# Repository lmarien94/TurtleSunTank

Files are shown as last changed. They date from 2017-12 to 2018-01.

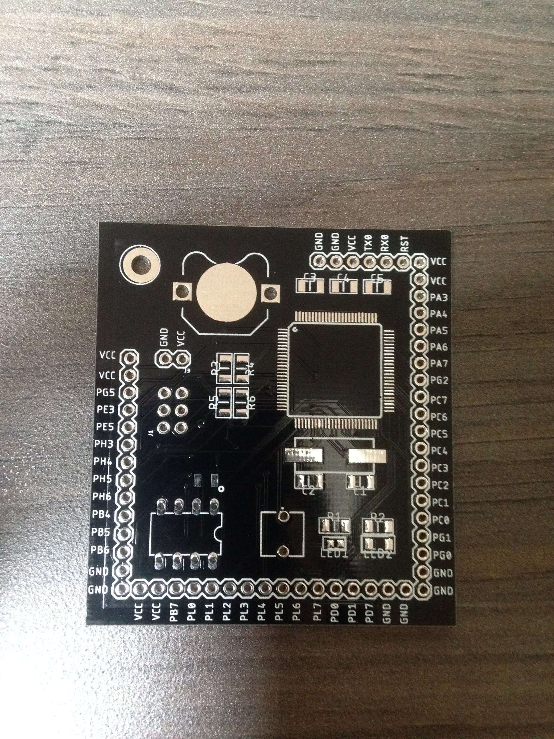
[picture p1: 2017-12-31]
Pictures/PCB before soldering.JPG

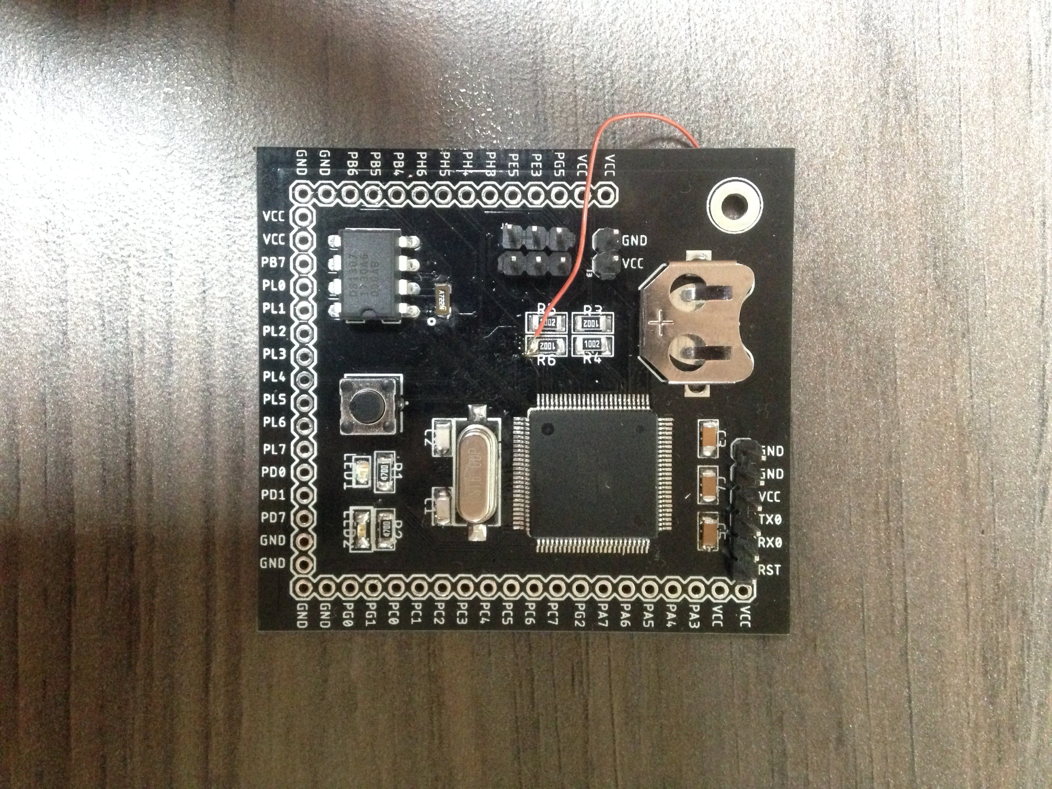
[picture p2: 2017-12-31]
Pictures/PCB after soldering.JPG

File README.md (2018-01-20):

# TurtleSunTank
Since reptiles are classified as ectothermic, which means that they are unable to regulate their body temperature internally and rely on the outer temperature. My turtles need a place to sun and with them growing their current sunningplace becomes a bit to small. Therefore I've designed an automated sun tank that can be placed on their current living space. Afcourse being an electronic enthousiast, the tank is fully automated.

It can perform the following tasks:
- Switch the lights automatically on/off based on the time,
- Adjust the lighting depending on the temperature & humidity in the sun tank,
- Switch the heating element for the water on/off based on the water temperature,
- Displaying the temperature & humidity in the sun tank on an LCD,
- Displaying the temperature of the water on an LCD.

For this project I've decided to design an small microcontroller based on an Atmega 2560 with an RTC on board:
PCB design

Major components used in this project:
- MCU: Atmega 2560
- RTC: DS1307
- temperature sensor: DS18B20 (waterproof version)
- temperature & humidity sensor: DHT11
- LCD: standard 16x2 I2C LCD
- Relay module: standard 2 channel relay module

The project contains the following folders:
- PCB design: here you can find everything of the PCB design.
- 3D printing & lasercutting: an OpenSCAD model of the enclossure I've build (based on the The Ultimate Parametric Box by Heartman) and the design of the plexiglass used for the turtle sun tank.
- Code: the code written for the project.

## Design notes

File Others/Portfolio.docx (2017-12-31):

UNIVERSITEIT ANTWERPEN

Academiejaar 2017-2018

Faculteit Toegepaste Ingenieurswetenschappen

I-Prototyping

Portfolio

Mariën Levi

Master of Science in de

industriële wetenschappen: elektronica-ICT

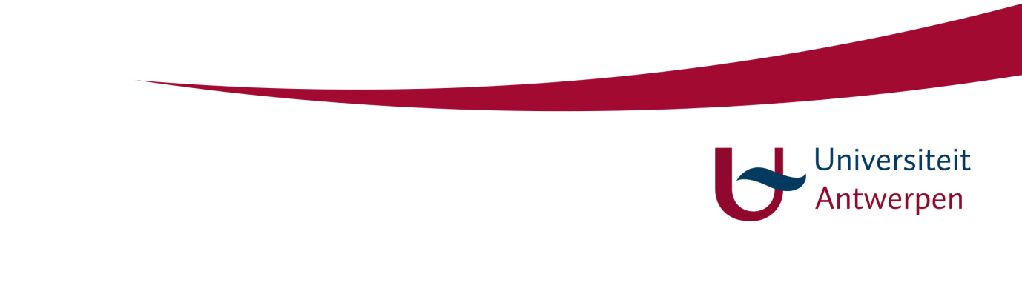
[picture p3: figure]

# 1 Algemene Inleiding

Het doel van het vak Prototyping bestond uit het aanleren van de basistechnieken rond de volgende disciplines:

- Lasercutten
- 3D printen
- PCB design/ontwerp

Er moest een project uitgewerkt worden waar deze 3 technieken in toegepast werden. Om deze reden werd er besloten om een geautomatiseerde zonnentank te bouwen voor waterschildpadden. In tegenstelling tot zoogdieren welke een constante lichaamstemperatuur hebben (met schommeling) en dus endothermisch zijn, zijn reptielen ectothermisch. Dit betekend dat zij geen constante lichaamstemperatuur hebben en maken gebruik van de zon om hun lichaamstemperatuur op te warmen en de grond om hun lichaam af te koelen. Het is daarom belangrijk dat reptielen genoeg toegang hebben tot warmte/zonlicht. Voor waterschildpadden is dit tevens ook belangrijk volledig op te kunnen drogen om schimmelinfecties te voorkomen.

Hieronder de specificaties van de zonnentank waarna er 3 aparte paragraven zullen volgen welke de 3 technieken in detail bespreken:

- De lichten dienen automatisch aan en uit te gaan op bepaalde tijdstippen van de dag (hier dient rekening gehouden te worden met het opkomen/ondergaan van de zon en winter/zomeruur).
- De warmtelamp dient aan/uit te gaan afhankelijk van de temperatuur en luchtvochtigheid in de zonnentank.
- Via een LCD display dient de luchtvochtigheid en temperatuur in de zonnentank gelezen te kunnen worden alsook de watertemperatuur en op welk uur van de dag de lampen op/afspringen.
- Het frame van de tank dient uit hout gebouwd te worden.
- De wanden worden in plexiglas ontworpen, er dienen genoeg luchtgaten voorzien te zijn alsook openingen voor het voederen van de beesten en een opening voor de lamp.
- Er dient een omhulsel voor de elektronica ontworpen te worden waar de verschillende bordjes in gehuisvest worden.

Onderstaande afbeeldingen geven een snel prototyping van het frame (en de bak) weer, dit wordt echter in de toekomst verbeterd maar vraagt een lange tijd gezien alles aan elkaar gelijmd wordt (met een minimaal aantal vijzen) waardoor de ontwikkeling van de echte tank zeer traag vlot (wegens het tekort aan sergeanten en het niet meer permanent wonen bij mijn ouders). Om deze reden zal er vlak voor het examen een “follow-up” portfolio zijn wat doorgestuurd zal worden aan de docenten met een ontwikkelportfolio van het eindresultaat betreffende het frame van de zonnentank zelf.

De verschillende files kunnen op mijn Github gevonden worden (denk hierbij aan de PCB design files, 3D print files, lasercut files alsook de code welke geschreven werd voor het project) onder de volgende link: https://github.com/lmarien94/TurtleSunTank.

Mariën Levi, 31/12/2017.

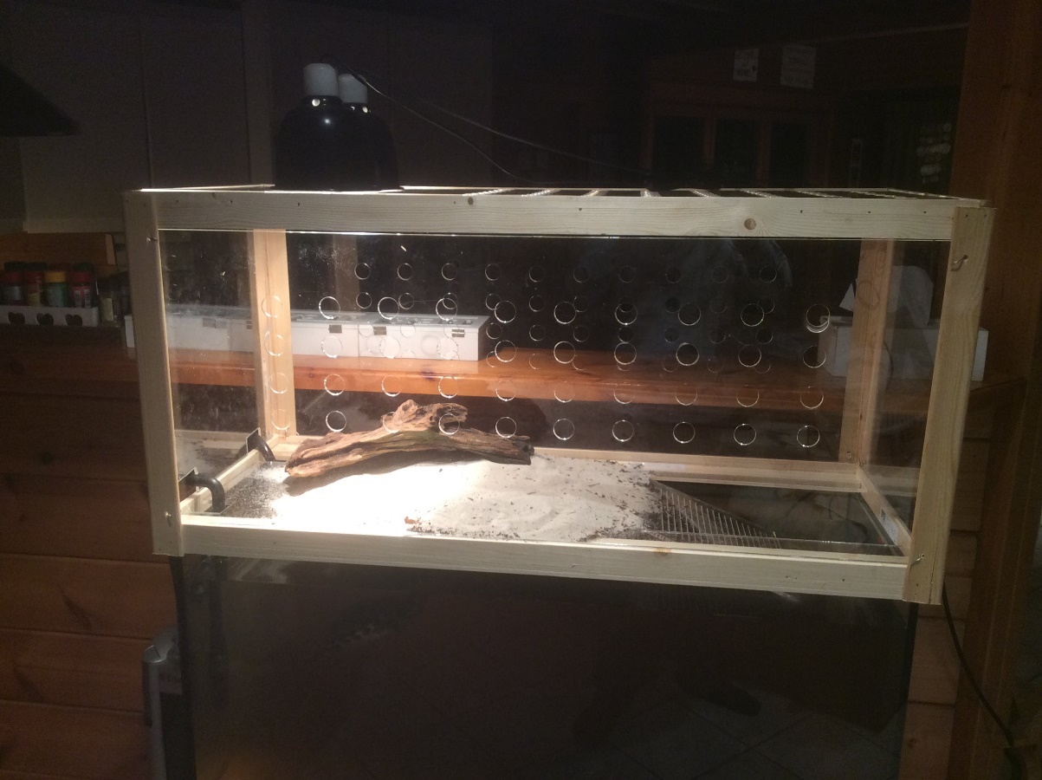
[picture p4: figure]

Figuur 1: prototyping zonnentank (vooraanzicht)

Figuur 2: prototyping zonnentank (zijaanzicht)

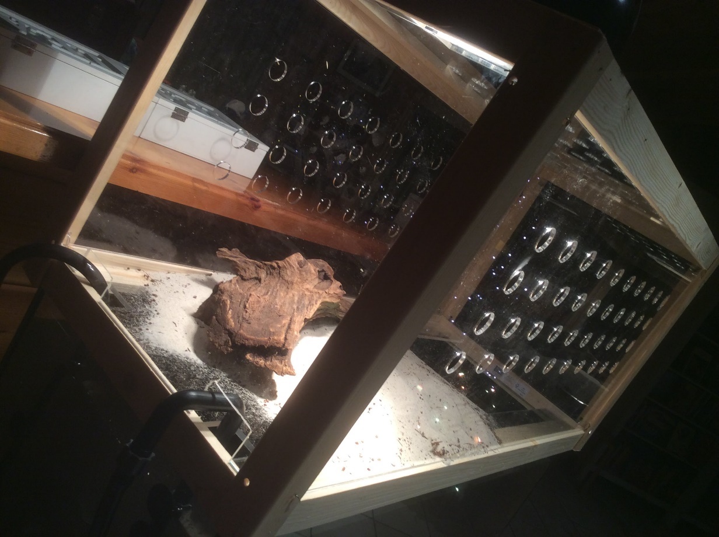
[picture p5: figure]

Figuur 3: prototyping zonnentank (zijaanzicht)

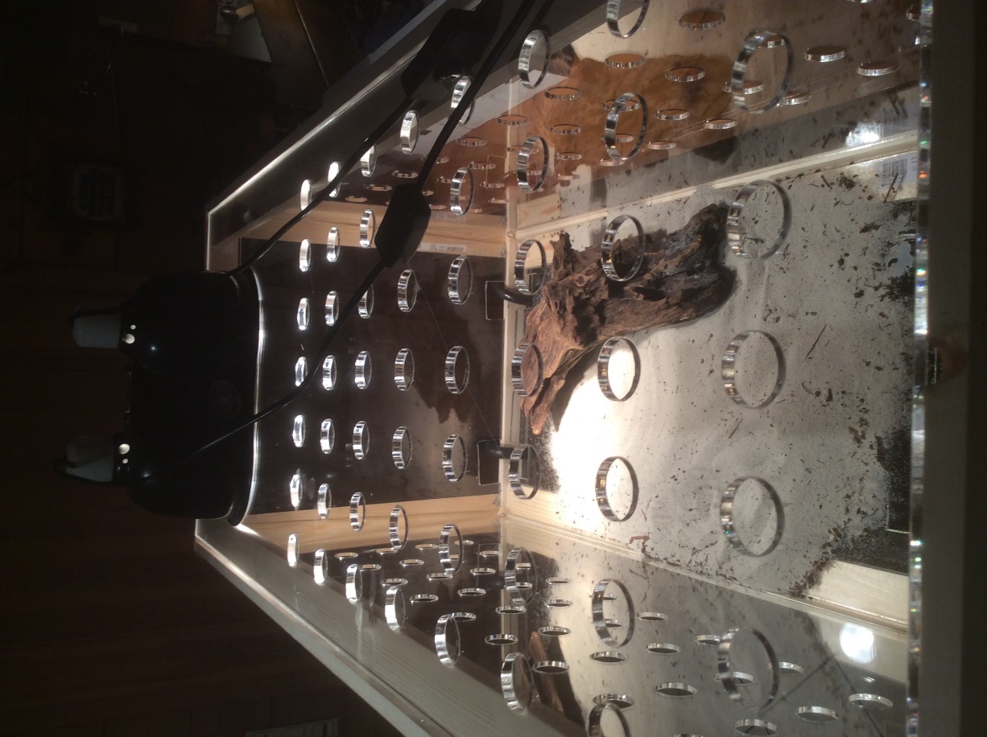
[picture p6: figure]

Figuur 4: prototyping zonnentank (bovenaanzicht)

# 2 PCB design/ontwerp

## 2.1 Inleiding

Voor het PCD Design/ontwerp werd er een microcontroller gebaseerd op een Atmega2560 ontwerpen. De motivatie om een eigen microcontroller te ontwerpen is de volgende:

- Een gewone Arduino Mega is in omvang te groot, niet alle pinnen dienen gebruikt te worden waardoor er veel plaats uitgewonnen kan worden door zelf een microcontroller te ontwerpen en deze in grootte te reduceren.
- Er werd gebruik gemaakt van een Atmega2560 vanwege de grootte die het aan boord heeft. In de toekomst is het de bedoeling een AC-dimmingsbord toe te voegen voor de lampen (en om dit aan te sturen dient er heel wat code uitgeschreven te worden). Om deze reden voldoet een Atmega328p (standaard arduino uno) niet qua geheugengrootte.
- Gezien de tijd bijgehouden moest worden (en de wens was geen gebruik van Wi-Fi te maken) diende er een RTC mee geïmplementeerd te worden op de microcontroller, door deze zelf te ontwerpen kon de RTC mee op het bordje gezet worden wat op zijn beurt weer plaats uitspaarden.

Gezien de ervaring hierin 0.0% was, diende er eerst in het geheel ingelezen te worden. De volgende referenties werden gebruikt om een gevoel voor het geheel te krijgen:

- Mr. Nick Gammon's How to make an Arduino-compatible minimal board (http://www.gammon.com.au/breadboard)
- TSJWang's DIY Arduino Mega 2560 or 1280 (https://www.instructables.com/id/DIY-Arduino-Mega-2560/)
- FuzzyStudio's DIY Bare Minimum Arduino Mega 2560 (http://www.instructables.com/id/DIY-Bare-Minimum-Arduino-Mega-2560/)

Een volgende referentie die geraadpleegd werd alvorens te beginnen aan het PCB design kwam van Atmel. Dit was een applicatie note (AVR042: AVR Hardware Design Considerations) en voorziet een draad voor de ontwerpen die gevolgd moet worden wanneer hardware ontworpen wordt die Atmel AVR microcontrollers aan boord heeft. Deze applicatie note kan gevonden worden op: http://www.atmel.com/Images/Atmel-2521-AVR-Hardware-Design-Considerations_ApplicationNote_AVR042.pdf.

## 2.2 Theoretische uiteenzetting

In deze sectie zal een kleine theoretische uiteenzetting gebeuren van wat er geleerd werd tijdens het raadplegen van bovenstaande referenties.

### 2.2.1 Reset pin op AVR’s

De reset pint op AVR microcontrollers is actief laag, dit wil zeggen dat de pin extern laag gezet dient te worden om de AVR te resetten. Deze pint heeft 2 doeleinden:

- Alle lijnen te verlossen door alle pinnen (uitgezonderd XTAL pinnen) in een tri-state te zetten, alle I/O registers te initialiseren en de programma teller op 0 te zetten.
- Om ervoor te zorgen dat de AVR in programmeer mode gaat.

De Reset lijn heeft een interne pull-up weerstand, echter kan in ruis rijke omgevingen deze inefficiënt zijn en een reset kan hierdoor sporadisch gebeuren. Daarom is het aan te raden een externe pull-up te gebruiken op de Reset lijn, deze voorkomt dan een ongewenst laag signaal de Reset triggert. De aangeraden weerstand hiervoor bedraagt 4.7kΩ. Om de Reset lijn van andere soorten ruis te beschermen zou er een condensator geconnecteerd moeten worden tussen de Reset pin en de grond maar wordt echter niet vereist gezien de AVR intern een laagdoorlaat filter aan boord heeft welke komaf maakt met pieken en ruis die een reset zouden kunnen veroorzaken. Indien High-Voltage/Parallel Programming (HVPP) gewenst is zou er ESD bescherming ingebouwd moeten worden door gebruik te maken van ESD bescherming dioden, echter wordt er van deze functie geen gebruik gemaakt.

Met het bovenstaande gezegd te hebben, wordt het volgende Reset Pin circuit aangeraden:

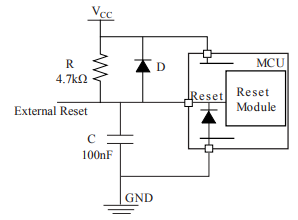
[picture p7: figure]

Figuur 5: aangeraden Reset Pin connecties

In het uiteindelijke design zullen de ESD dioden en condensator uiteindelijk wegvallen gezien deze niet specifiek nodig zijn.

### 2.2.2 Connecteren Programmeer lijnen

Atmel AVR microcontrollers voorzien 1 of meerdere interfaces voor programeren of debugging. In-System Programming (ISP) is een programmeer interface welke gebruikt wordt voor het programeren van Flash, EEPROM, Lock-bits, … Gezien er gebruikt gemaakt wordt van een nieuwe chip, is er geen boatloader aanwezig. Om deze op de Atmega2560 te zetten dient de Serial Peripheral Interface (SPI) programeer interface voor ISP gebruikt te worden. Er zijn door Atmel ISP programmers 2 soorten standaarden betreffende SPI connectoren (6-pins en 10-pins):

In dit geval zal er gebruikt worden gemaakt van de 6-pin programeer header. Indien andere apparaten geconnecteerd zijn aan de ISP lijnen is het aangeraden series weerstanden mee te plaatsen om op deze manier de programmer te beschermen. Dit wordt gedaan als volgt:

Figuur 6: bescherming van de programmer

Echter is dit voor dit geval niet van toepassing en kunnen de SPI lijnen gewoon naar buiten uitgebroken worden.

### 2.2.3 Kristal oscillatoren

Voor de oscillator kan er gekozen worden tussen een kristal -of keramische oscillator. Even een korte opsomming van de voor -en nadelen van beide:

- De keramische oscillatoren zijn een in lagere kost en kwaliteit variant van de kristal oscillatoren.
- De Q-factor van een keramische oscillator is lager als dat van een kristal oscillator (dit kan beide een voor -en nadeel zijn, afhankelijk van de toepassing).
- Gezien de Q-factor lager is bij een keramische oscillator kan deze gemakkelijker getuned worden in een specifieke frequentie.
- De keramische oscillator is gevoeliger aan temperatuur en load veranderingen ten opzichte van een kristal oscillator waardoor de kans van ongewenste frequentie varianties groter is.
- Keramische oscillatoren hebben een snellere start-up als kristal oscillatoren.

De parallelle resonantie wordt in circuits gebruikt die reactieve componenten bezitten (bv. condensatoren). Zo’n circuits zijn afhankelijk van de reactieve componenten en de resonantie om de fase verandering teweeg te brengen die de oscillator start en onderhoudt op een bepaalde frequentie. Elementaire oscillator circuits die gebruikt worden voor parallelle resonanties worden voorgesteld in onderstaande afbeelding:

Figuur 7: elementaire inverteer circuits equivalent aan de oscillator circuits in AVR

Het gedeelde boven de gestreepte lijn stelt een oscillator schema voor zoals deze te vinden zijn in AVR. En de ingebouwde oscillator cricuits in AVR kunnen begrepen worden als een inverteer gebaseerd oscillator circuit welke in bovenstaande figuur voorgesteld wordt.

De linkse variant is een oscillator circuit voor kristal en keramische oscillatoren die sneller als 400kHz zijn, de rechte is een circuit voor lage frequentie kristallen (32.768kHz) maar worden niet in AVR gebruikt. Het verhaal gaat verder met de linkse variant van het circuit.

Voor zulke circuits is het nodig om externe capacitieve ladingen aan te brengen. De grootte hiervan is afhankelijk van het kristal dat gebruikt wordt. Indien deze waarde te groot is kan het zijn dat de oscillator niet zal starten. Daarom dient er in de datasheet van de oscillator naar de waarde van de capacitieve load (CL) gekeken te worden. De waarde van de condensatoren kan dan aan de hand van volgende vergelijking berekend worden:

C_L = (C^(') _(L1) *C'_(L2))/(C^(') _(L1) +C'_(L2))

Waarbij geld dat:

C^(') _(L1) = C_(L1) +C_(L1S) en C^(') _(L2) = C_(L2) +C_(L2)

CL1 en CL2 verwijzen naar de externe condensatoren en CL1S en CL2S verwijzen naar de capaciteit van de oscillator lijnen. Indien een symmetrische layout gebruikt wordt zal gelden dat CL1 = CL2 = CL1S = CL2C = CS waarbij CS genomen kan worden tussen de 5pF à 10pF. Hierdoor kunnen de externe condensatoren berekend worden als volgt:

C=2* C_L -C_S

### 2.2.4 Real Time Clock (RTC)

Voor de RTC werd er gebruik gemaakt van een DS1307, het schema dat hierrond gebouwd werd, werd rechtstreeks vanuit de datasheet van de corresponderende RTC gehaald. Hier waren verder geen aanpassingen nodig. Volgend schema werd geïmplementeerd:

Figuur 8: schema RTC

## 2.3 Echtelijk PCB design/ontwerp

Na het verwerken van bovenstaande theorie werd het volgende initiële schema ontwikkeld:

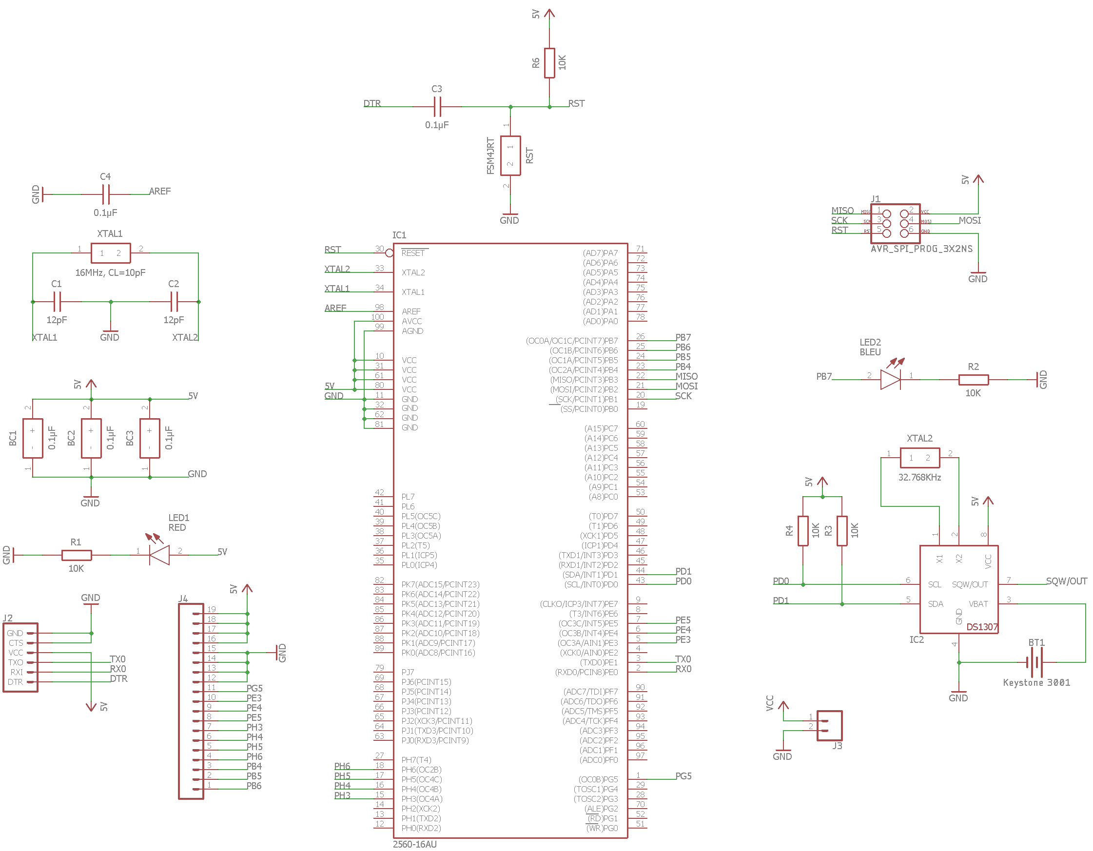
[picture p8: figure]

Figuur 9: initieel schema PCB design

Wat gepaard ging met het volgende PCB design:

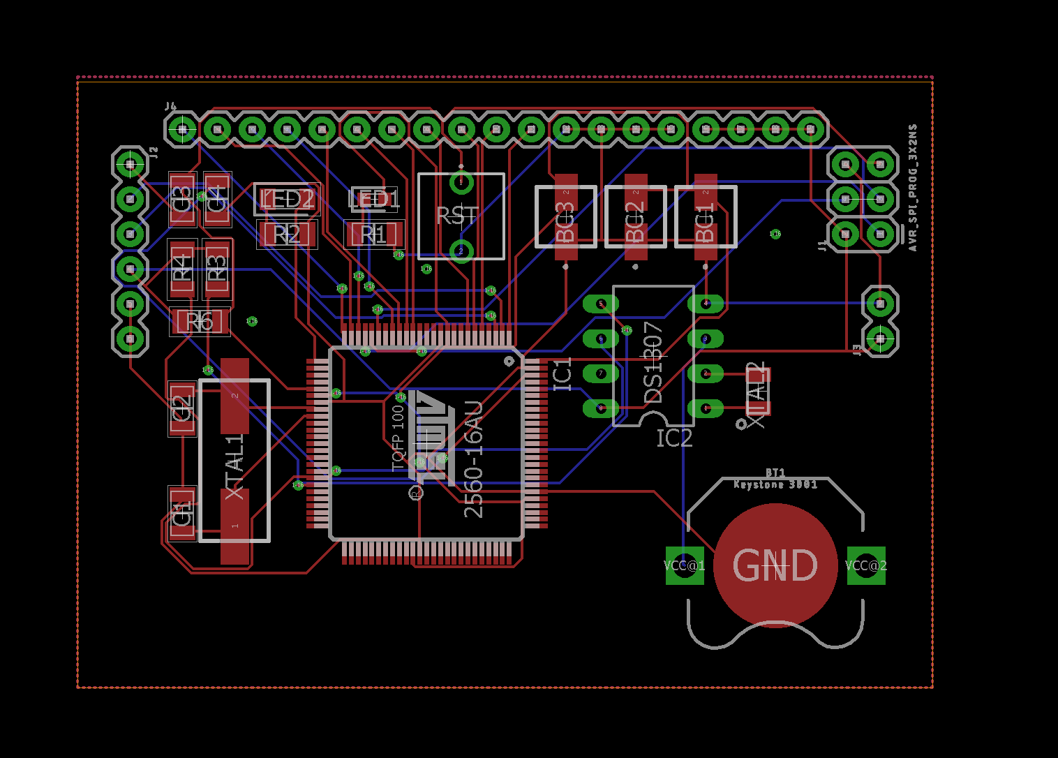
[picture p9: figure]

Figuur 10: initieel board design

Echter waren er met dit ontwerp een aantal problemen:

- De weerstanden op de LED’s waren te hoog, hierdoor ging er te weinig stroom door de LED’s.
- De ontkoppelcondensator op de reset knop was onnodig (zie puntje 2.1.1).
- Er werden te weinig digitale pinnen naar buiten gestuurd.

Met de verkregen feedback werd daarom het volgende schema ontworpen:

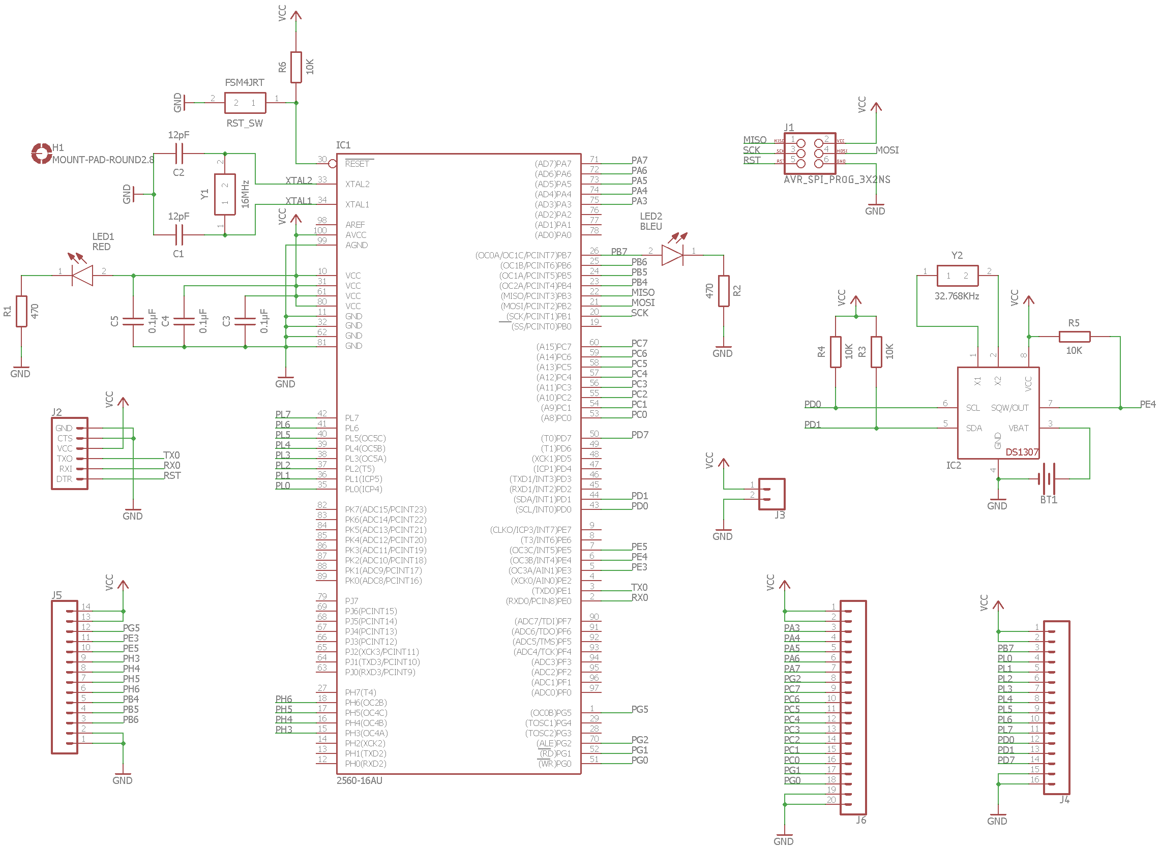
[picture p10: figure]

Figuur 11: finaal ontwerp schema

Dit leidde tot het volgende board design:

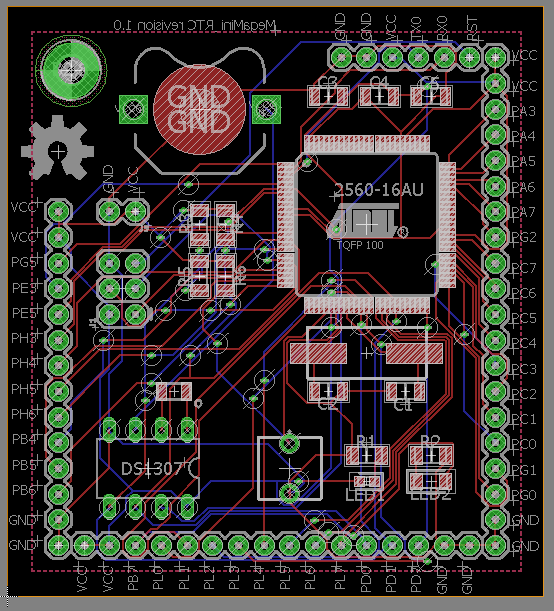
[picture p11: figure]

Figuur 12: finaal board design

Na productie leidde dit tot het volgende bordje:

Figuur 13: PCB na productie

En na solderen resulteerde dit in het volgende:

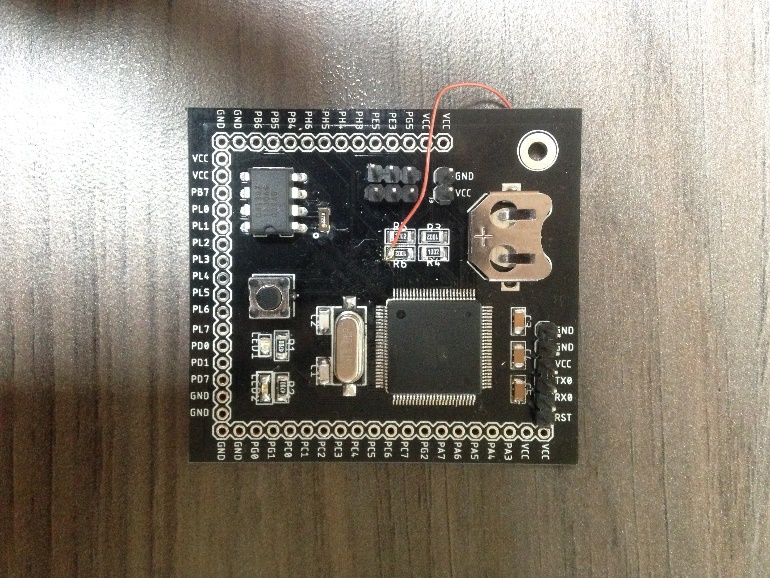
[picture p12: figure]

Figuur 14: PCB na solderen

## 2.4 Moeilijkheden ondervonden

Over het algemeen waren er geen moeilijkheden ondervonden, er was echter 1 kleine fout in het PCB geïmplementeerd en had betrekking tot het doorverbinden van de Reset pin met de SPI header. Hierdoor diende er manueel een draadverbinding gesoldeerd te worden, echter eens deze gesoldeerd werd werkte alles naar behoren.

## 2.5 PCB files en code

Zoals reeds in de inleiding vernoemd werd kunnen de schema’s en de PCB board design files alsook de code gevonden worden op mijn Github onder de volgende adressen: https://github.com/lmarien94/TurtleSunTank/tree/master/PCB_design en https://github.com/lmarien94/TurtleSunTank/tree/master/Code.

Op het examen zelf zal er een demo van het geheel gegeven worden.

# 3 Lasercutten

## 3.1 Inleiding

De wanden van de zonnentank zullen in plexiglas ontworpen worden. Deze moeten voorzien worden van luchtgaten en een gat voor de verlichting alsook dient er een brug gevormd te worden opdat de schildpadden van het water gedeelde naar het land gedeelde kunnen.

Er waren een paar aspecten waar rekening gehouden mee diende te worden:

- De dikte van de wanden zelf maakten niet veel uit gezien het houten frame het gewicht van de zonnentank overdraagt op het glazen aquarium.
- De bovenplaat diende wel dik genoeg te zijn opdat deze ondanks alle lucthgaten en gat voor de lampen toch nog structureel sterk genoeg was zodat deze niet ging doorbuigen.
- De onderplaat waar het zand op komt te liggen dient dik genoeg te zijn om doorbuiging te voorkomen maar niet te dik opdat de oploopbrug niet meer geplooid kan worden.

Met dit in het achterhoofd werd er besloten de zijwanden in 3mm dik plexiglas te doen waarop de boven- en onderkant gebouwd werden met 6mm plexiglas.

## 3.2 Metalcut ontwerpen

Volgende designs werden in Metalcut ontworpen:

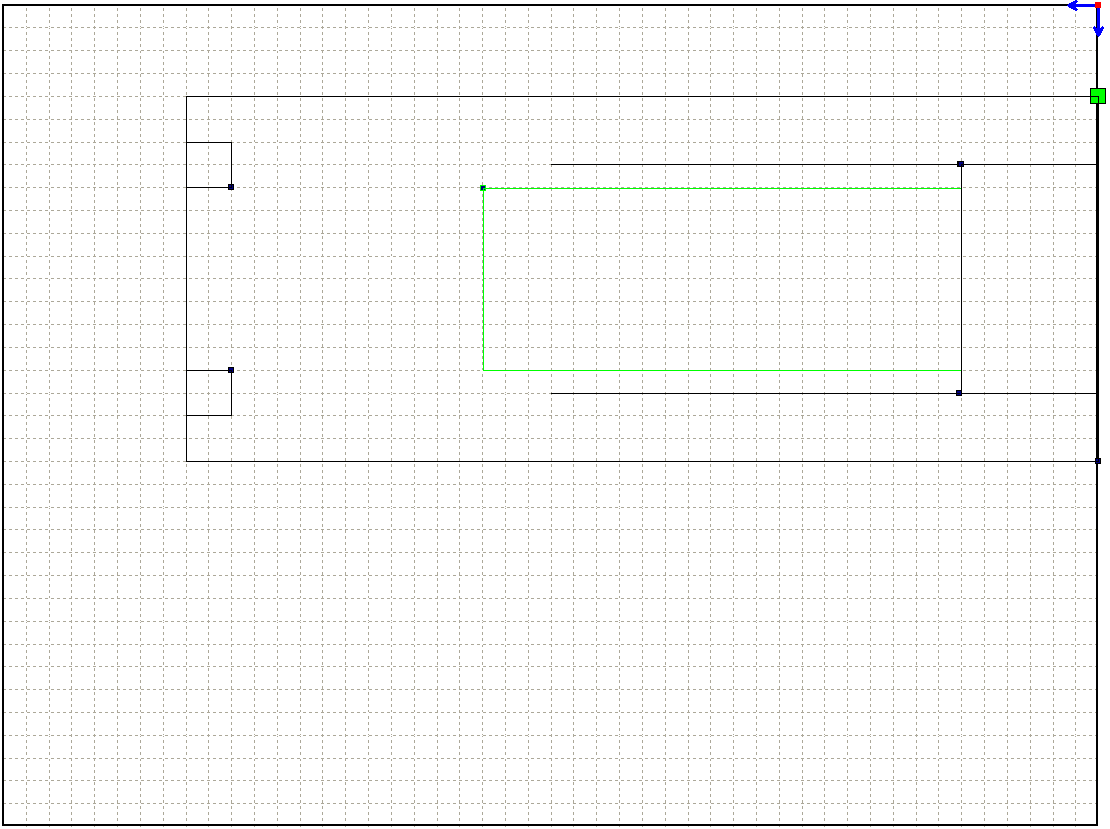
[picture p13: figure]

Figuur 15: bodemplaat finaal

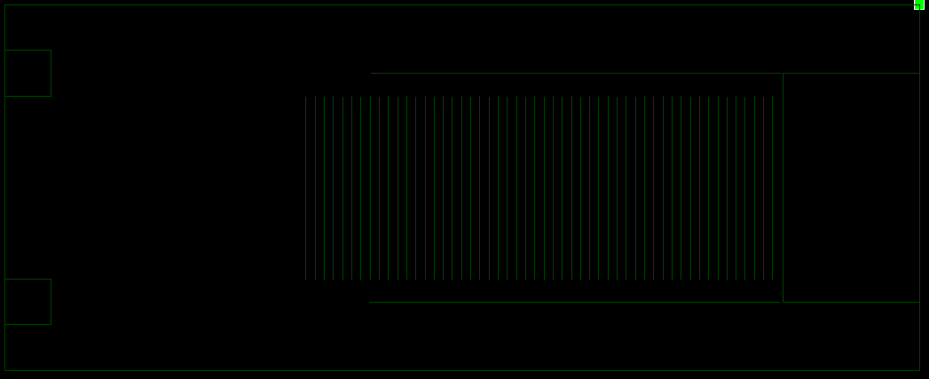
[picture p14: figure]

Figuur 16: bodemplaat simulatie

Gezien de schildpadden een goede grip nodig hadden op het bruggetje om uit het water te klimmen werden hiervoor groeven gegraveerd in het plexiglas van ongeveer een 2mm dik met 1 cm ruimte tussen elke groeve. Dit kon bereikt worden door de volgende instellingen te gebruiken:

Figuur 17: instellingen graveren

Eens het geheel af was werd er door middel van een heatgun een buiging aangebracht in het plexiglas om de brug te bekomen zoals deze te zien is op figuur 1 en 2 in de inleiding.

De bovenplaat zag er als volgt uit:

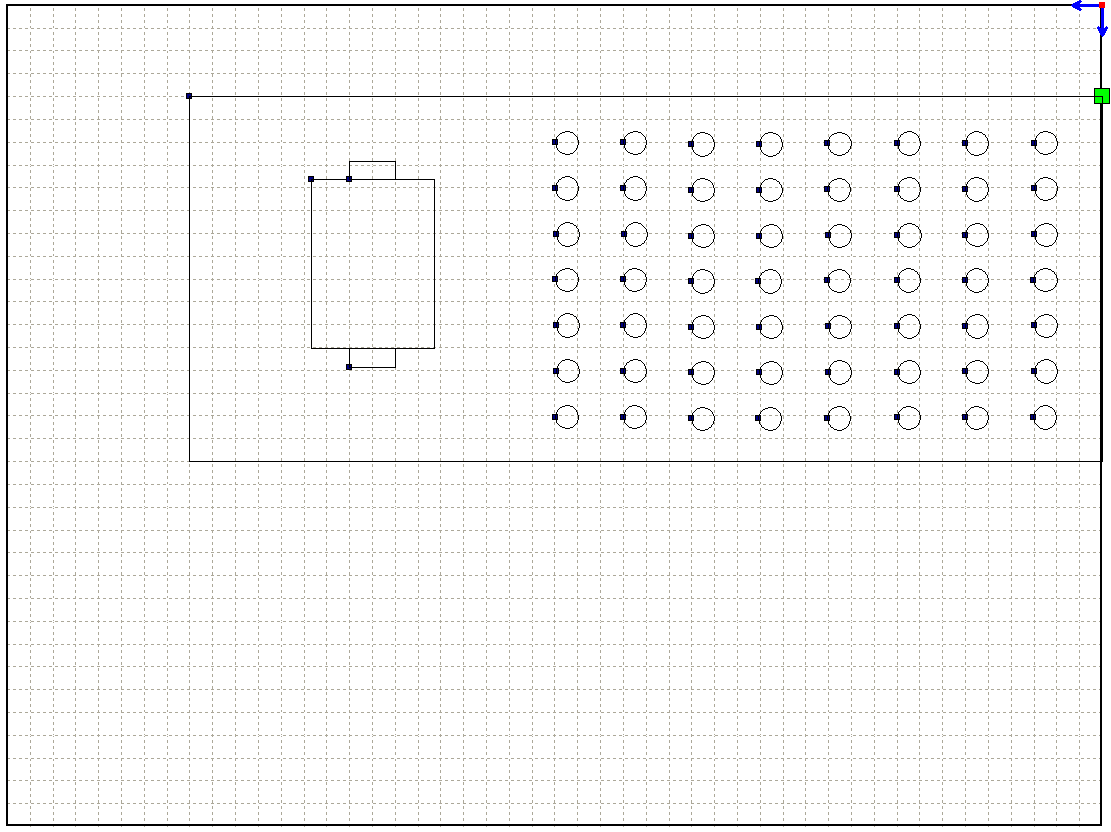
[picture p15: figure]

Figuur 18: bovenplaat finaal

Luchtgaten werden aangebracht aan de rechterkant gecombineerd met 1 groter gat waar het armatuur van de lampen op kan staan wat ervoor zorgt dat er een gat voorzien is opdat de warmte van de lampen en het UV licht de binnenkant van de zonnentank bereiken.

De grote zijplaten zagen er als volgt uit (hiervan werden 2 stuks geproduceerd):

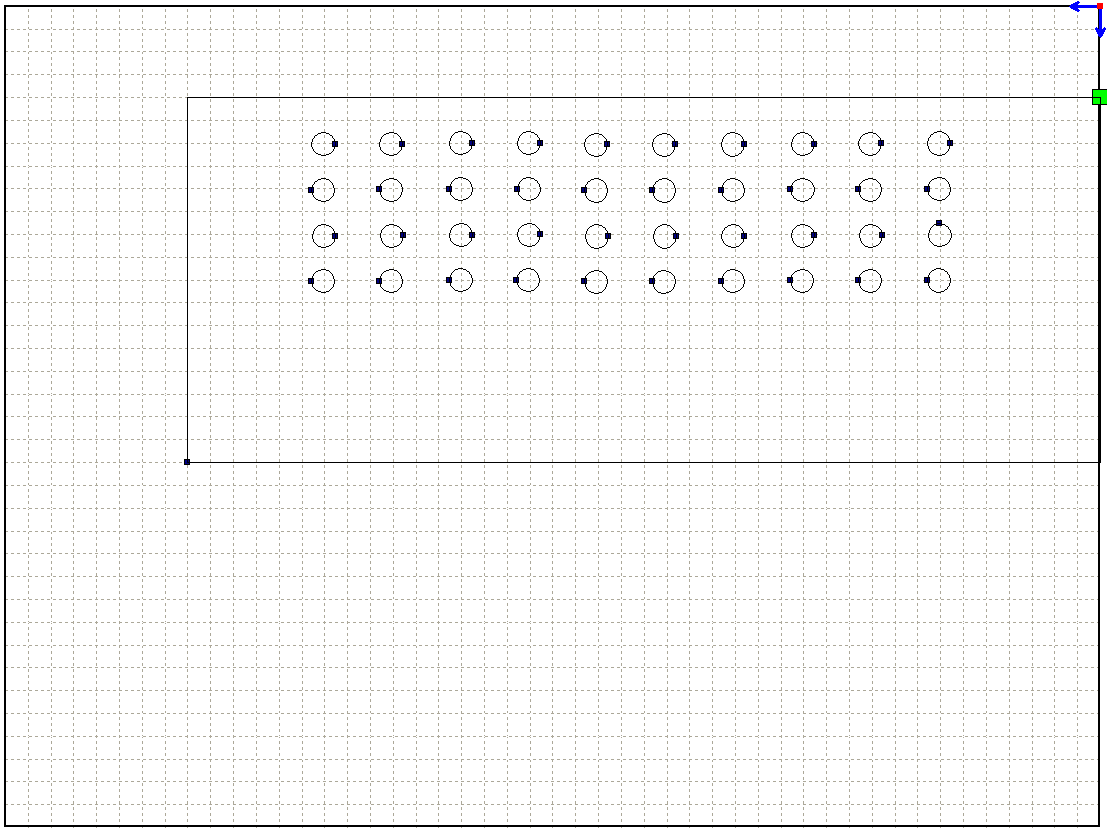
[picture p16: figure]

Figuur 19: zijplaten finaal

De reden dat de luchtgaten zo hoog zitten heeft te maken met het feit dat er op deze manier geen zand door de gaten kan komen wat vuiligheid met zich mee brengt.

De kleine zijwanden dienden geen graveringen of gaten te hebben waardoor dit niets meer is als een rechthoek van 400 * 400 mm. Om deze reden zullen deze eenvoudige aspecten ook niet meer besproken worden in het portfolio.

## 3.3 Moeilijkheden ondervonden

De voornaamste moeilijkheid van dit zat hem in de bodemplaat. Dit bruggetje diende een correcte hoek te hebben en mocht niet te lang of te kort zijn opdat de schildpadden op een comfortabele manier in en uit het water konden. Ondanks de vele probeersels was het zeer moeilijk dit in orde te krijgen.

Het eerste ontwerp zorgde ervoor dat de schildpadden niet comfortabel op het droge konden doordat het laatste stuk niet gegraveerd werd en hierdoor schoven ze er telkens af.

Het tweede (en ook finaal design dat hier mee in het portfolio opgenomen werd) zorgde ervoor dat vanwege het volledig ingraveren (ook waar de buiging plaats diende te vinden) het plexiglas structureel te zwak werd voor te verwarmen en buigen. Hierdoor brak het geheel waardoor besloten werd om de bodem van hout te maken en het idee van plexiglas achterwegen te laten.

Hoe deze bodem juist ontworpen werd en welk materiaal hierbij gebruikt werd zal omschreven worden in het “follow-up” portfolio zoals in de inleiding verteld werd.

## 3.4 Lasercut files

Zoals reeds in de inleiding vernoemd werd kunnen de .rdl files van Metalcut gevonden worden op mijn Github onder het volgende adres: https://github.com/lmarien94/TurtleSunTank/tree/master/Lasercutting.

# 4 3D printen

## 4.1 Inleiding

Voor het 3D printen zal er een behuizing ontworpen worden welke de elektronica huisvesting. Hierin dienen 2 bordjes te komen:

- Het ontworpen PCB,
- Een AC relay switch board dat gebruikt wordt voor het aan/uit schakelen van de lampen.

Gezien er gebruik gemaakt wordt van een AC relay switching bord is het thermische aspect belangrijk om in achting te nemen en hiervoor zullen er in het design een reeks verluchtingsgaten voorzien worden opdat er een natuurlijke luchtstroom gecreëerd kan worden. Een ander vereiste is dat er bekabelingsgaten voorzien worden opdat de bekabeling van de lampen, sensoren en het bord zelf op een handige manier kunnen verlopen.

Het design zelf is gebaseerd op “The Ultimate Parametric Box” van Heartman. Deze behuizing was exact wat mijn vereiste waren op het meer modulair maken en aan paar aanpassingen van de code na.

Het voordeel van dit geheel is dat de behuizing symmetrisch is waardoor aanpassingen die zowel op boven als onderkant gebeuren niet 2x dienen te gebeuren maar met 1 aanpassing de gehele behuizing mee veranderd.

## 4.2 Ronding module

Deze module is het meest elementaire in het gehele design. Indien deze aangeroepen wordt zal er een kubus met specifieke (door de gebruiker gedefinieerd) gemaakt worden welke afgeronde zijkanten heeft. Dit wordt bereikt d.m.v. de minkowski functie. Zoals in de OpenSCAD user Manual/Transformations omschreven staat dienen er eerst 2 objecten geïnitialiseerd te worden:

Figuur 20: minkowski voorbeeld (1)

Vervolgens kan de gebruiker een minkowski optelling van beide objecten doen wat resulteerd in het volgende:

Figuur 21: minkowski voorbeeld (2)

Belangrijk is om te beseffen dat de dimensies van het geheel veranderen (gezien er een optelling gebeurd werd). Indien de cilinder een straal heeft van 2 eenheden en de kubus een breedte van 10 eenheden zal de nieuwe afmeting 14 eenheden bedragen (10 + 2 + 2, vanwege elke kant).

De code van de Rounding module ziet er als volgt uit:

//Deze module zal een balk produceren en afhankelijk van de fillet waarde

//zullen de hoeken minder of meer afgerond zijn.

module ronding($a=lengte, $b=breedte, $c=hoogte) {

translate([0,fillet, fillet]){

minkowski() {

cube([$a-(lengte/2), $b-(2*fillet), $c-(2*fillet)], center = false);

rotate([0,90,0]) {

cylinder(r=fillet, h=lengte/2, center = false);

}

}

}

}

De ronding module met de minimale fillet waarde (0.1):

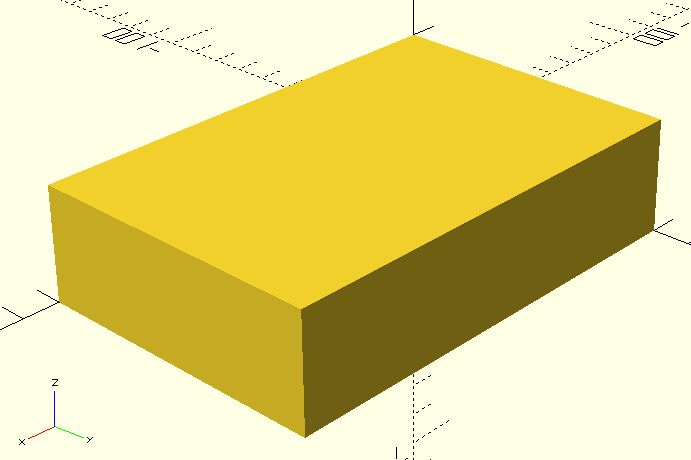
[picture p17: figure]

Figuur 22: ronding module met kleine fillet

De ronding module met de maximale fillet waarde (12):

Figuur 23: ronding module met grote fillet

## 4.3 Doos module

Deze module zal de elementaire behuizing produceren zonder ventilatiegaten, pootjes, … De ronding module zal aangeroepen worden en de doos module zal de ronding uithollen en ook de top afsnijden opdat er enkel een doos overblijft.

De code kan gevonden worden onder de doos module in het OpenSCAD project. En deze produceert het volgende:

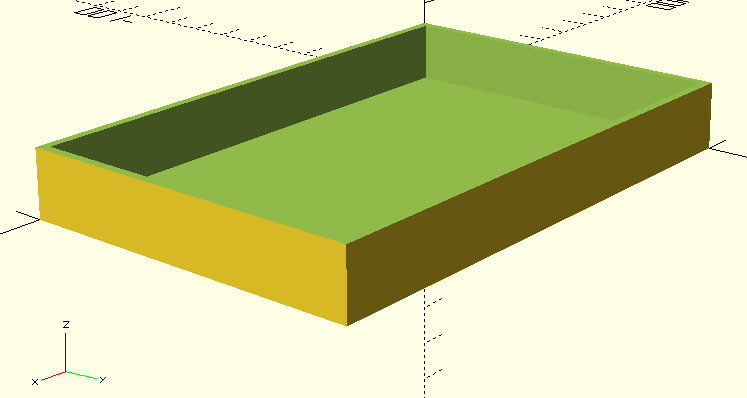
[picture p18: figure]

Figuur 24: doos module

## 4.4 Bevestiging module

De bevestiging module zal ervoor zorgen dat er een bevestiging gemaakt worden tussen de boven -en onderkant. Hiervoor heeft de gebruiker de keuze of deze ronde of kubusvormige bevestigingen wenst. Vervolgens worden de onderkanten eraf gesneden om interferentie met de luchtgaten te voorkomen.

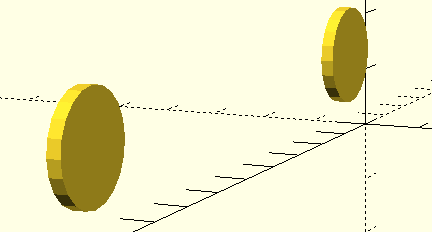
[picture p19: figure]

Figuur 25: bevestiging zonder afsnijding

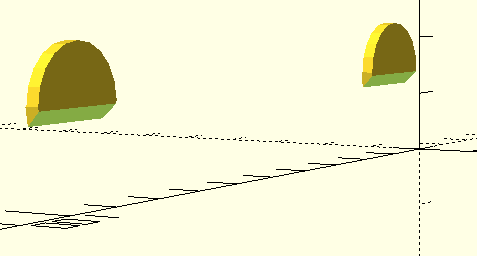
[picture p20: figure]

Figuur 26: bevestiging na afsnijding

De code kan gevonden worden onder de bevestiging module in het OpenSCAD project.

Om beide aan elkaar te koppelen dient er een unie tussen de doos en bevestiging gemaakt te worden in OpenSCAD, wat resulteert in het volgende tussenresultaat:

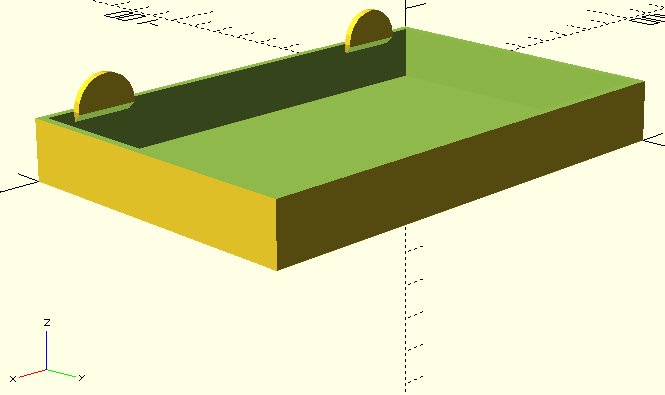
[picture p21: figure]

Figuur 27: behuizing met bevestiging

## 4.5 Ventilatiegaten module

Deze module zal zorgen voor de ventilatiegaten. Er zijn 2 soorten (deze voor de onderkant en bovenkant). Het verschil tussen beide is dat de onderkant een opening heeft waar kabels door kunnen en de bovenkant heeft smalle ventilatiegaten. Aan de hand van een parameter kan de gebruiker meegeven of er ventilatiegaten voor de onderkant of bovenkant dienen gemaakt te worden.

Figuur 28: ventilatiegaten voor bovenkant

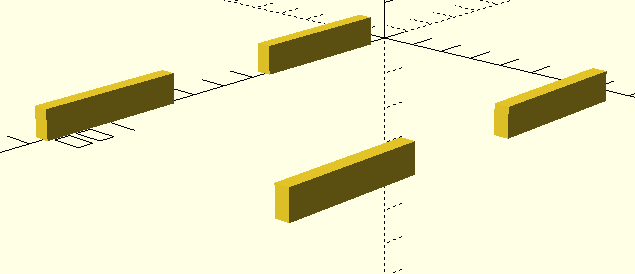
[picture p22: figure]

Figuur 29: ventilatiegaten onderkant

Vervolgens dienen de ventilatiegaten van het geheel afgetrokken te worden om de openingen te produceren in de behuizing, dit geeft volgend tussenresultaat:

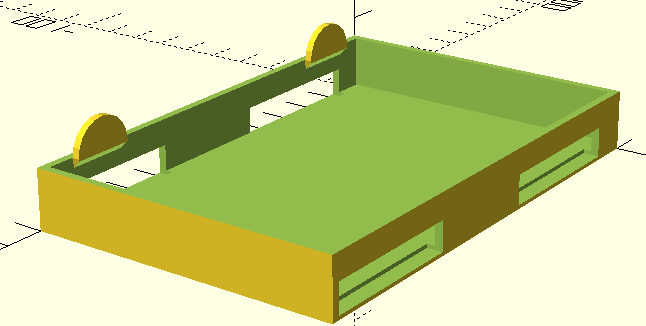
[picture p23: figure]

Figuur 30: behuizing met bevestiging

## 4.6 Gaten module

Deze module zorgt voor de gaten in de bevestigingen en de behuizing zelf opdat deze schroeven kunnen aanvaarden. Dit zijn niets meer als cilindervormige gaten met een bepaalde diameter welke afgetrokken dienen te worden van het geheel, dit resulteert in het volgende:

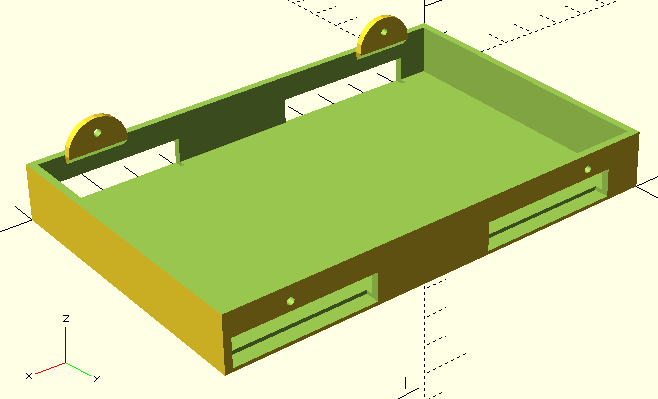
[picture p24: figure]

Figuur 31: behuizing met bevestigingsgaten

## 4.7 Het geheel

Al het voorgenoemde zal resulteren in de volgende behuizing:

Figuur 32: complete behuizing (1)

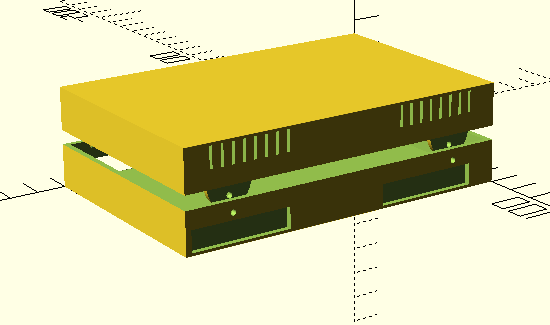
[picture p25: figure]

Figuur 33: complete behuizing (2)

## 4.8 OpenSCAD files

Zoals reeds in de inleiding vernoemd werd kunnen de benodigde files gevonden worden op mijn Github op het volgende adres: https://github.com/lmarien94/TurtleSunTank/tree/master/3D%20printing.

Gezien het geheel nog niet geprint is kan ik nog niets over de echtelijke implementatie zeggen, hierop hoop ik spoedig van u een email te kunnen ontvangen dat het geheel klaar is.

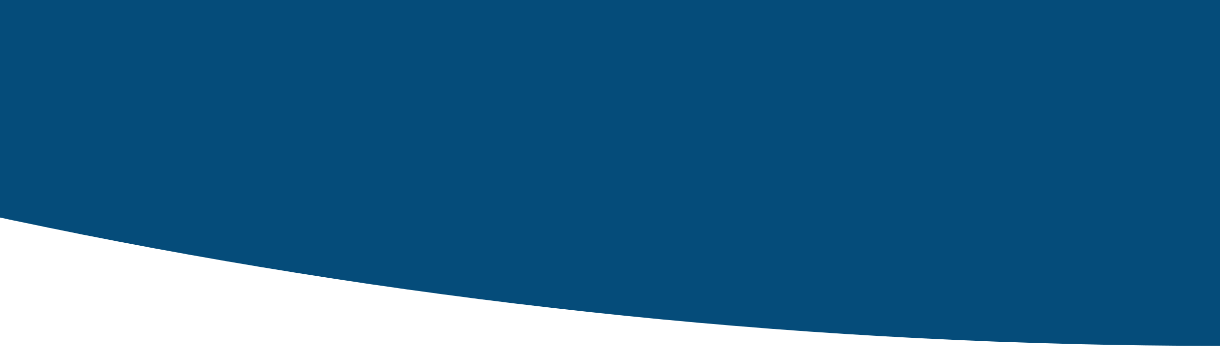
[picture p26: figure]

I-Prototyping UA-FTI-EI

naam vakUA-FTI

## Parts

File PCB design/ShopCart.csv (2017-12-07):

Artikelnr. | Ordercode | RoHS-compatibel? | Opmerkingen | Hoeveelheid | Artikelnummer fabrikant | Naam fabrikant | Fabrikant / beschrijving | Beschikbaarheid | Prijs per stuk | Artikelprijs | Prijs na korting
1 | 1288330 | YES |  | 1.0 | ATMEGA2560-16AU | MICROCHIP | Controller Family/Series:ATmega; CPU Speed:16MHz; Program Memory Size:256KB; RAM Memory Size:8KB; No. of Pins:100Pins; MCU Case Style:TQFP; No. of I/O's:86I/O's; Embedded Interface Typ | 1339 | 10.3700 | 10.37
2 | 1414715 | YES |  | 10.0 | C1206C104K5RACTU | KEMET | Ceramic Capacitor Case:1206 [3216 Metric]; Capacitance:0.1µF; Voltage Rating:50V; Capacitance Tolerance:± 10%; Dielectric Characteristic:X7R; Product Range:C Series; Packaging:Cut Tape; | 168865 | 0.0537 | 0.54
3 | 2322071 | YES |  | 1.0 | 150060RS75000 | WURTH ELEKTRONIK | LED Colour:Red; LED Mounting:SMD; Bulb Size:-; Forward Current If:30mA; Forward Voltage:2V; Wavelength Typ:625nm; Luminous Intensity:250mcd; Viewing Angle:140°; Lens Shape:Rectangular; Pack | 24946 | 0.1660 | 0.17
4 | 2307726 | YES |  | 10.0 | ERJ8ENF4700V | PANASONIC ELECTRONIC COMPONENTS | Resistance:470ohm; Voltage Rating:200V; Resistor Case Style:1206 [3216 Metric]; Power Rating:250mW; Resistance Tolerance:± 1%; Product Range:ERJ8E Series; Packaging:Cut Tape; Resis | 1999 | 0.0399 | 0.40
5 | 2063983 | YES |  | 1.0 | FOXSDLF/160-20 | FOX ELECTRONICS | Frequency Nom:16MHz; Crystal Case:SMD, 11.7mm x 5mm; Frequency Stability + / -:50ppm; Load Capacitance:20pF; Frequency Tolerance + / -:30ppm; Product Range:HC49SDLF Series; Operating Temperat | 483 | 0.3010 | 0.30
6 | 1650892 | YES |  | 10.0 | C1206C120J5GACTU | KEMET | Ceramic Capacitor Case:1206 [3216 Metric]; Capacitance:12pF; Voltage Rating:50V; Capacitance Tolerance:± 5%; Dielectric Characteristic:C0G / NP0; Product Range:C Series; Packaging:Cut | 4658 | 0.1680 | 1.68
7 | 2396052 | YES |  | 1.0 | FSM4JRT | ALCOSWITCH - TE CONNECTIVITY | Illumination:Non Illuminated; Contact Voltage DC Nom:24V; Contact Current Max:50mA; Operating Force:160gf; Switch Terminals:Through Hole; Product Range:FSMJRT Series; SVHC:No SVHC (12-J | 36201 | 0.0930 | 0.09
8 | 2307295 | YES |  | 10.0 | ERJ8ENF1002V | PANASONIC ELECTRONIC COMPONENTS | Resistance:10kohm; Voltage Rating:200V; Resistor Case Style:1206 [3216 Metric]; Power Rating:250mW; Resistance Tolerance:± 1%; Product Range:AEC-Q200 ERJ8E Series; Packaging:Cut Tap | 11810 | 0.0329 | 0.33
9 | 2322084 | YES |  | 1.0 | 150120BS75000 | WURTH ELEKTRONIK | LED Colour:Blue; LED Mounting:SMD; Bulb Size:-; Forward Current If:30mA; Forward Voltage:3.2V; Wavelength Typ:470nm; Luminous Intensity:145mcd; Viewing Angle:140°; Lens Shape:Rectangular; | 3945 | 0.3100 | 0.31
10 | 1278036 | YES |  | 1.0 | Q13FC13500004 FC-135 32.768KHZ 12.5PF | EPSON | Frequency Nom:32.768kHz; Crystal Case:SMD, 3.2mm x 1.5mm; Frequency Stability + / -:-; Load Capacitance:12.5pF; Frequency Tolerance + / -:20ppm; Product Range:FC-135 Series; Operatin | 12884 | 1.6300 | 1.63
11 | 908642 | YES |  | 1.0 | 3001 | KEYSTONE | Battery Sizes Accepted:Coin Cell - 12mm; Battery Terminals:PCB Pins; Contact Material:Phosphor Bronze; Contact Plating:Nickel Plated Contacts; Product Range:-; SVHC:No SVHC (20-Jun-2016); | 1185 | 3.3900 | 3.39
 |  |  |  |  |  |  | Subtotaal | 19.21
 |  |  |  |  |  |  | Totaal aantal goederen | 19.21
 |  |  |  |  |  |  | Standaard | 0.00
 |  |  |  |  |  |  | BTW | Onbekend
 |  |  |  |  |  |  | Totaal | 19.21

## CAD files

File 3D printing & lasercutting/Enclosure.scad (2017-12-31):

$fn=20;

/******     Parameter lijst     ******/
/*************************************/
//Afmetingen doos
lengte = 120;
breedte = 80;
hoogte = 30;
dikte = 2;

//Fillet waarde
//De Fillet waarde zal voor kleine waarden scherpe hoeken geven
//en voor grote waarden ronde hoeken. Het bereik ligt tussen 0,1 en 12.
fillet = 0.1;

//Ventilatiegaten
ventilatiegatenSpacingBoven = 1;
ventilatiegatenSpacingOnder = 8;
//Zorgen dat de ventilatiegaten door de behuizing komen
ventilatiegatenDikte = dikte*2;
//De lengte van de ventilatiegaten
ventilatiegatenLengte = dikte*2;

//Bevestiging
bevestigingDiameterCilinder = 16;
//0.8 om te vermenigvulden met een integer om zo de correcte 
//M-waarde van een schroef te krijgen
schroefgatendiameterCilinder = 0.8;






//Deze module zal een balk produceren en afhankelijk van de fillet waarde
//zullen de hoeken minder of meer afgerond zijn.
module ronding($a=lengte, $b=breedte, $c=hoogte) {
    translate([0,fillet, fillet]){
        minkowski() {
            cube([$a-(lengte/2), $b-(2*fillet), $c-(2*fillet)], center = false);
            rotate([0,90,0]) {
                cylinder(r=fillet, h=lengte/2, center = false);
            }
        }
    }
}

//Deze module zal de elementaire behuizing produceren zonder ventilatiegaten, pootjes, ...
module doos() {
    //De 0.000001 is toegevoegd om de bug in OpenSCAD te elimineren
    dikte = dikte*2+0.000001;
    difference() {
        difference() {
            union(){
                //Het uithollen van de doos
                difference(){
                    ronding();
                    translate([dikte/2, dikte/2, dikte/2]) {
                        ronding($a=lengte-dikte, $b=breedte-dikte, $c=hoogte-dikte);
                    }
                }
            }
         //Het afsnijden van de top opdat enkel de randen overblijven
         translate([-dikte, -dikte, hoogte/2]){
             cube([lengte+dikte, breedte+dikte, hoogte], center=false);
         }
     }
 }
 }

//Deze module zal de bevestiging produceren welke op de behuizing gezet wordt
 module bevestiging() {
     dikte = dikte*2;
     difference() {
         //hier worden 2 cilindervomige bevestigingen gemaakt
         union() {
             translate([3*dikte + 5, dikte, hoogte/2]) {
                 rotate([90,0,0]){
                 cylinder(d=bevestigingDiameterCilinder, dikte/2);
                 }
             }
             translate([lengte-((3*dikte) + 5), dikte, hoogte/2]) {
                 rotate([90,0,0]){
                 cylinder(d=bevestigingDiameterCilinder, dikte/2);
                 }
             }
         }
         //Snij de onderkant eraf met een hoek van 45°
         translate([4,dikte+fillet, hoogte/2-57]){
             rotate([45,0,0]){
             cube([lengte, 40, 40]);
             }
         }
         translate([0,-(dikte*1.46), hoogte/2]){
             cube([lengte, dikte*2, 10]);
             }
         }
     }

//Deze module produceert gaten afhankelijk van de M-variant de gebruiker wilt
// Voor M3 geef een parameter 3 mee, voor M4 een parameter 4, enz. enz.
module gaten(M) {
    dikte = dikte*2;
    union() {
        translate([3*dikte+5,20,hoogte/2+4]){
            rotate([90,0,0]){
            cylinder(d=schroefgatendiameterCilinder*M,20);
            }
        }
        translate([lengte-((3*dikte)+5),20,hoogte/2+4]){
            rotate([90,0,0]){
            cylinder(d=schroefgatendiameterCilinder*M,20);
                    }
                }
        translate([3*dikte+5,breedte+5,hoogte/2-4]){
            rotate([90,0,0]){
            cylinder(d=schroefgatendiameterCilinder*M,20);
            }
        }
        translate([lengte-((3*dikte)+5),breedte+5,hoogte/2-4]){
            rotate([90,0,0]){
                cylinder(d=schroefgatendiameterCilinder*M,20);
            }
        }
    }
}

//Deze module produceert ventilatiegaten en krijgt een parameter mee of het de 
//bovenkant of onderkant is (verschillende ventilatiegaten worden geproduceerd
//afhankelijk hiervan).
 module ventilatiegaten(top) {
     union() {
         //Indien het om de bovenkant gaat
         if(top == 1) {
             for(i=[0:dikte:lengte/4]){
                 translate([10+i,-ventilatiegatenDikte+ventilatiegatenLengte,1]){
                    cube([ventilatiegatenSpacingBoven,ventilatiegatenDikte,hoogte/4]);
                 }
                 translate([(lengte-10) - i,-ventilatiegatenDikte+ventilatiegatenLengte,1]){
                    cube([ventilatiegatenSpacingBoven,ventilatiegatenDikte,hoogte/4]);
                 }
                 translate([(lengte-10) - i,breedte-ventilatiegatenLengte,1]){
                    cube([ventilatiegatenSpacingBoven,ventilatiegatenDikte,hoogte/4]);
                 }
                 translate([10+i,breedte-ventilatiegatenLengte,1]){
                    cube([ventilatiegatenSpacingBoven,ventilatiegatenDikte,hoogte/4]);
                 }
             }
         }

     if(top == 0) {
         for(i=[0:dikte:lengte/4]){
             translate([10+i,-ventilatiegatenDikte+ventilatiegatenLengte,1]){
                 cube([ventilatiegatenSpacingOnder,ventilatiegatenDikte,hoogte/4]);
             }
             translate([(lengte-10) - i,-ventilatiegatenDikte+ventilatiegatenLengte,1]){
                 cube([ventilatiegatenSpacingOnder,ventilatiegatenDikte,hoogte/4]);
             }
             translate([(lengte-10) - i,breedte-ventilatiegatenLengte,1]){
                 cube([ventilatiegatenSpacingOnder,ventilatiegatenDikte,hoogte/4]);
             }
             translate([10+i,breedte-ventilatiegatenLengte,1]){
                 cube([ventilatiegatenSpacingOnder,ventilatiegatenDikte,hoogte/4]);
             }
         }
     }
 }
 }

//doos();
//bevestiging();
//gaten();
//ventilatie();

/******     Onderkant     ******/
//Het verschil nemen tussen de doos met bevestigingen en de
//ventilatiegaten en bevestigingsgaten.
difference() {
        //Samenvoegen van de doos met de bevestiging.
        union() {
            doos();
            bevestiging();
        }
    gaten(3);
    ventilatiegaten(0);
}

/******     Bovenkant     ******/
translate([0,breedte, hoogte+10]){
    rotate([0,180,180], center = true) {
        difference() {
            union() {
                doos();
                bevestiging();
            }
            gaten(3);
            ventilatiegaten(1);
        }
    }
}

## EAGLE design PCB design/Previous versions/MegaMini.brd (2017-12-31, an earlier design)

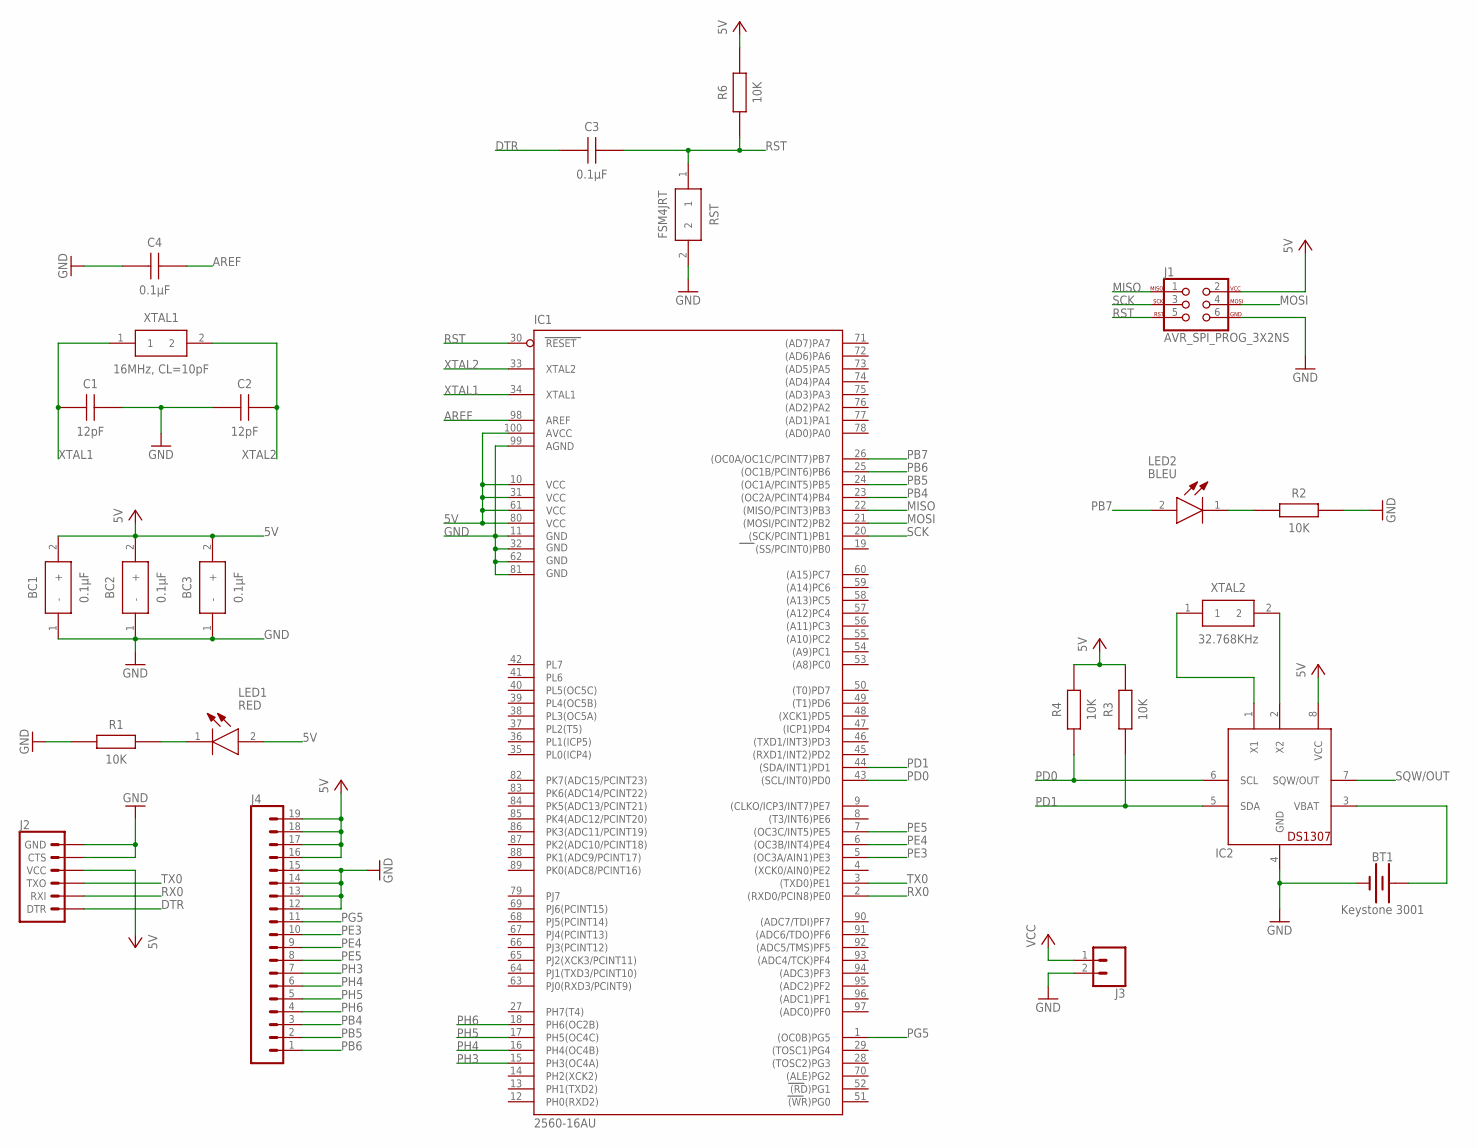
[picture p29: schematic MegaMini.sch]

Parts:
BC1, BC2, BC3: 0.1µF; 865230640001
BT1: Keystone 3001; BATTCON_12MM_PTH
C1, C2: 12pF; CAPC3216X88N
C3, C4: 0.1µF; CAPC3216X90N
IC1: 2560-16AU; TQFP100
IC2: DS1307; DIL08
J1: AVR_SPI_PROG_3X2NS; 2X3-NS
J2: 6_PIN_SERIAL_TARGET; 1X06
J3: CONN_02; 1X02
J4: CONN_19; 1X19
LED1: RED; LEDC1608X80N
LED2: BLEU; LEDC3214X78N
R1, R2, R3, R4, R6: 10K; RESC3116X70N
RST: FSM4JRT
XTAL1: 16MHz, CL=10pF; FOXSDLF/120-20
XTAL2: 32.768KHz; FC-135

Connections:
5V: BC1.2 (+), BC2.2 (+), BC3.2 (+), IC1.10 (VCC), IC1.31 (VCC1), IC1.61 (VCC2), IC1.80 (VCC3), IC1.100 (AVCC), LED1.2 (A)
AREF: C4.2, IC1.98 (AREF)
DTR: C3.1, J2.1 (DTR)
GND: BC1.1 (-), BC2.1 (-), BC3.1 (-), BT1.GND (-), C1.2, C2.1, C4.1, IC1.11 (GND), IC1.32 (GND1), IC1.62 (GND2), IC1.81 (GND3), IC1.99 (AGND), IC2.4 (GND), J1.6, J2.5 (CTS), J2.6 (GND), J3.2, J4.12, J4.13, J4.14, J4.15, R1.1, R2.1, RST.2
MISO: IC1.22 ((MISO/PCINT3)PB3), J1.1
MOSI: IC1.21 ((MOSI/PCINT2)PB2), J1.4
unnamed: LED1.1 (K), R1.2
unnamed: LED2.1 (K), R2.2
unnamed: IC2.1 (X1), XTAL2.1
unnamed: IC2.2 (X2), XTAL2.2
unnamed: BT1.VCC@1 (+), IC2.3 (VBAT)
PB4: IC1.23 ((OC2A/PCINT4)PB4), J4.3
PB5: IC1.24 ((OC1A/PCINT5)PB5), J4.2
PB6: IC1.25 ((OC1B/PCINT6)PB6), J4.1
PB7: IC1.26 ((OC0A/OC1C/PCINT7)PB7), LED2.2 (A)
PD0: IC1.43 ((SCL/INT0)PD0), IC2.6 (SCL), R4.1
PD1: IC1.44 ((SDA/INT1)PD1), IC2.5 (SDA), R3.1
PE3: IC1.5 ((OC3A/AIN1)PE3), J4.10
PE4: IC1.6 ((OC3B/INT4)PE4), J4.9
PE5: IC1.7 ((OC3C/INT5)PE5), J4.8
PG5: IC1.1 ((OC0B)PG5), J4.11
PH3: IC1.15 (PH3(OC4A)), J4.7
PH4: IC1.16 (PH4(OC4B)), J4.6
PH5: IC1.17 (PH5(OC4C)), J4.5
PH6: IC1.18 (PH6(OC2B)), J4.4
RST: C3.2, IC1.30 (RESET), J1.5, R6.1, RST.1
RX0: IC1.2 ((RXD0/PCIN8)PE0), J2.2 (RXI)
SCK: IC1.20 ((SCK/PCINT1)PB1), J1.3
SQW/OUT: IC2.7 (SQW/OUT)
TX0: IC1.3 ((TXD0)PE1), J2.3 (TXO)
VCC: IC2.8 (VCC), J1.2, J2.4 (VCC), J3.1, J4.16, J4.17, J4.18, J4.19, R3.2, R4.2, R6.2
XTAL1: C1.1, IC1.34 (XTAL1), XTAL1.1
XTAL2: C2.2, IC1.33 (XTAL2), XTAL1.2

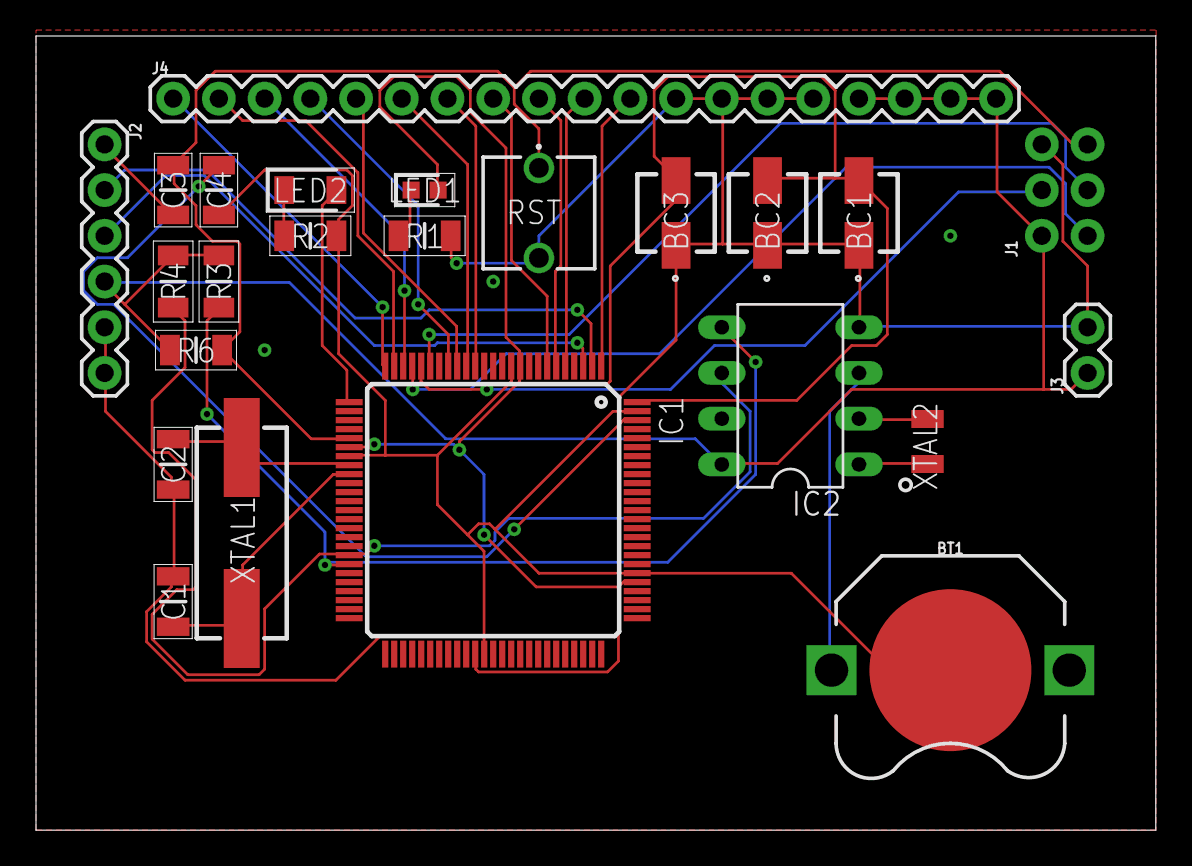
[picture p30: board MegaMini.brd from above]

Board: 2 copper layers, 62.2 x 44.1 mm, 24 parts (0 on the bottom side), 32 nets.

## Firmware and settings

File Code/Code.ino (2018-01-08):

/**
 * The code for the turtle tank
 * author: Levi Mariën
 */
#include <dht.h>
#include <Wire.h>
#include <OneWire.h>
#include <DallasTemperature.h>
#include <LiquidCrystal_I2C.h>
#include <LiquidCrystal.h>
#include <RTClib.h>

#include "tabel.h"

#define DS18B20_PIN 9
#define DHT11_PIN 10
#define RELAY_PIN1 11
#define RELAY_PIN2 12
#define LCD_I2C_ADDRESS 0x27
#define TEMPERATURE_LAMP_ON   21
#define TEMPERATURE_LAMP_OFF  25

//Set the LCD I2C address and pins on the I2C chip used for LCD connections.
LiquidCrystal_I2C lcd(LCD_I2C_ADDRESS, 2, 1, 0, 4, 5, 6, 7, 3, POSITIVE);
RTC_DS1307 rtc;
OneWire oneWire(DS18B20_PIN);
DallasTemperature sensors(&oneWire);
dht DHT;

void calculateMainState();
void errorState();
int getTemperatureSunTank();
void displayTempAndHum();
void displayTempWater();
void switchRelayOnOff(bool switchOnOff);

//The different states for the state machine
enum MainStates {
        Day,              //Day state
        Night,            //Night state
        Error             //Error state
};
enum DayStates {
        DisplayTempAndHumidity, //Display the temperature and humidity of the sun tank
        DisplayTempWater, //Display the temperature of the water
        SwitchOffLamp,    //Switch off the lamp
        SwitchOnLamp      //Switch on the lamp
};

enum NightStates {
        sleep,
        wakeUp
};

enum MainStates mainState;
enum DayStates dayState;
enum NightStates nightState;

char daysOfTheWeek[7][12] = {"Sunday", "Monday", "Tuesday", "Wednesday", "Thursday", "Friday", "Saturday"};
int temperatureSunTank;
int temperatureWater;
int check;

void setup(){

        Serial.begin(9600);
        lcd.begin(16,2);
        pinMode(RELAY_PIN1, OUTPUT);
        sensors.begin();
        if (!rtc.begin()) {
                Serial.println("Couldn't find RTC");
                while (1) ;
        }

        calculateMainState();

        if (!rtc.isrunning()) {
                Serial.println("RTC is NOT running!");
                // following line sets the RTC to the date & time this sketch was compiled
                rtc.adjust(DateTime(F(__DATE__), F(__TIME__)));
                // This line sets the RTC with an explicit date & time, for example to set
                // January 21, 2014 at 3am you would call:
                // rtc.adjust(DateTime(2014, 1, 21, 3, 0, 0));
        }
}

/**
 * This function pulls the time of the RTC and sets the Day or Night state
 */
void calculateMainState() {

        DateTime now = rtc.now();
        Serial.print(now.year(), DEC);
        Serial.print('/');
        Serial.print(now.month(), DEC);
        Serial.print('/');
        Serial.print(now.day(), DEC);
        Serial.print(" (");
        Serial.print(daysOfTheWeek[now.dayOfTheWeek()]);
        Serial.print(") ");
        Serial.print(now.hour(), DEC);
        Serial.print(':');
        Serial.print(now.minute(), DEC);
        Serial.print(':');
        Serial.print(now.second(), DEC);
        Serial.println();

        mainState = Day;
        if (mainState == Day) {
                dayState = DisplayTempAndHumidity;
        }
}

void errorState() {
        lcd.clear();
        lcd.setCursor(0,0);
        lcd.print("!!Error!!");
        lcd.setCursor(0,1);
        lcd.print("!!Error!!");
}
int getTemperatureSunTank() {
        check = DHT.read11(DHT11_PIN);
        return (int)DHT.temperature;
}

void displayTempAndHum() {
        check = DHT.read11(DHT11_PIN);

        //Print to LCD
        lcd.clear();
        lcd.setCursor(0,0);
        lcd.print("Temp: ");
        lcd.print(DHT.temperature);
        lcd.print((char)223);
        lcd.print("C");
        lcd.setCursor(0,1);
        lcd.print("Humidity: ");
        lcd.print(DHT.humidity);
        lcd.print("%");

        //Display on Serial
        Serial.print("Temperature = ");
        Serial.println(DHT.temperature);
        Serial.print("Humidity = ");
        Serial.println(DHT.humidity);

}

void displayTempWater() {

        sensors.requestTemperatures();
        lcd.clear();
        lcd.setCursor(0,0);
        lcd.print("Water Temp: ");
        lcd.setCursor(0,1);
        lcd.print(sensors.getTempCByIndex(0));
        lcd.print((char)223);
        lcd.print("C");

        Serial.print("Water temperature = ");
        Serial.println(sensors.getTempCByIndex(0));

}
void switchRelayOnOff(bool switchOnOff) {

//If switchOnOff is true --> switch on lamp
//if switchOnOff is false --> switch off lamp
        if (switchOnOff) {
                digitalWrite(RELAY_PIN1, 0);
        } else {
                digitalWrite(RELAY_PIN1, 1);
        }
}

void loop()
{
        //calculateMainState();

        if (mainState == Day) {
                if (dayState == DisplayTempAndHumidity) {
                        displayTempAndHum();
                        delay(500);
                        Serial.print("State: DisplayTempAndHumidity");
                        Serial.println();
                        dayState = DisplayTempWater;
                        delay(500);
                } else if (dayState == DisplayTempWater) {
                        displayTempWater();
                        delay(500);
                        Serial.print("State: DisplayTempWater");
                        Serial.println();
                        temperatureSunTank = getTemperatureSunTank();
                        delay(500);
                        if (temperatureSunTank >= TEMPERATURE_LAMP_OFF) {
                                dayState = SwitchOffLamp;
                                delay(500);
                        } else if (temperatureSunTank <= TEMPERATURE_LAMP_ON) {
                                dayState = SwitchOnLamp;
                                delay(500);
                        } else {
                                calculateMainState();
                                delay(500);
                        }
                } else if (dayState == SwitchOffLamp) {
                        switchRelayOnOff(false);
                        delay(500);
                        Serial.print("State: SwitchOffLamp");
                        Serial.println();
                        calculateMainState();
                        delay(500);
                } else if (dayState == SwitchOnLamp) {
                        switchRelayOnOff(true);
                        delay(500);
                        Serial.print("State: SwitchOnLamp");
                        Serial.println();
                        calculateMainState();
                        delay(500);
                }
        } else if (mainState == Night) {


        } else {
                errorState();
        }
}

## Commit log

2017-11-12 Finished revision 1.0 of the schematic
    [MegaMini.sch]
2017-11-13 Finished the schematic
    [MegaMini.sch]
2017-11-14 revision 1.0 pcb design
    [MegaMini.brd, MegaMini.sch]
2017-11-14 Finished revision 1.0 PCB and some major changes to the schematic
    [MegaMini.brd, MegaMini.sch]
2017-11-16 Some little improvements to the pcb
    [MegaMini.brd]
2017-11-17 Adjustements on the Atmel2560 package
    [MegaMini.sch]
2017-11-18 Added silkscreen, finished design.
    Everything is finished, generating gerber files for the board house.
    [MegaMini.brd]
2017-11-18 Generated gerber files
    [MegaMini.GBL, MegaMini.GBO, MegaMini.GBP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]
2017-11-23 Starting with the design of the 3D print
    [enclosure.scad]
2017-11-28 Some small adjustements to the 3D print
    [MegaMini.brd, enclosure.scad]
2017-12-07 Added top for lasercutting
    [ShopCart.csv]
2017-12-10 Added some more lasercut files
2017-12-11 changed the screwholes in the top pannel
2017-12-31 Small adjustments
    [MegaMini.GBL, MegaMini.GBO, MegaMini.GBP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]
2017-12-31 Added some files and deleted others
    [MegaMini.GBL, MegaMini.GBO, MegaMini.GBP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]
2017-12-31 Added the enclosure for 3D printing
    [Behuizing.scad, enclosure.scad]
2017-12-31 Finished the portfolio and enclosure for 3D printing
    [Behuizing.scad]
2018-01-07 Reorganized the repository
    [Enclosure.scad]
2018-01-08 Edited error with RST in PCB

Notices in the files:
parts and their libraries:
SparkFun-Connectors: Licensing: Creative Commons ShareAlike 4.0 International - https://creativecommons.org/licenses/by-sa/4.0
